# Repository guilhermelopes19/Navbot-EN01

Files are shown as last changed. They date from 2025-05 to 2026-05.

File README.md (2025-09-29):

# NavBot-EN01 Wheeled_leg-Robot

| Real Robot | 3D Design |
| --- | --- |
|  |  |

[Physical Demo Showcase](https://www.youtube.com/watch?v=H16f_6Kxv-E)  

[3D Demo Showcase](https://www.youtube.com/watch?v=OKktbMr_LOk)  

### Mechanical Structure Documentation
Under the ["Hardware/RebotModel"](Hardware/RebotModel) folder:
* The file "OriginalRobotModel.stp" is the robot model file.
* 3D printing, carbon fiber cutting, and CNC processing can all directly use the files in the corresponding folders.
* In ["BOM.xlsx"](Hardware/RebotModel/BOM.xlsx), there are other small components that need to be purchased.

### PCB Documentation

* The project requires the fabrication of four PCBs. Both the schematic and PCB source files are provided, and the design environment used is [easyeda](https://www.easyeda.com/).
Import project reference ["Hardware/PCB/README"](Hardware/PCB/README.md)
* The main control board is based on the ESP32, with the brushless motor driver chip being the L6234PD013TR. 
* The encoder chip used is the AS5600, communicating with the main control board via the I2C interface.
* The IMU used is the MPU6050 module, which shares the same I2C interface with the right-side encoder.
* The servo debugging board combines two UART serial lines into one signal line using time-division multiplexing for data transmission and reception.
* Two SH1.0mm 4PIN double-ended cables which need to be purchased separately，with a recommended length of 15cm. 

    | Wire Connection | 
    | ------------ |
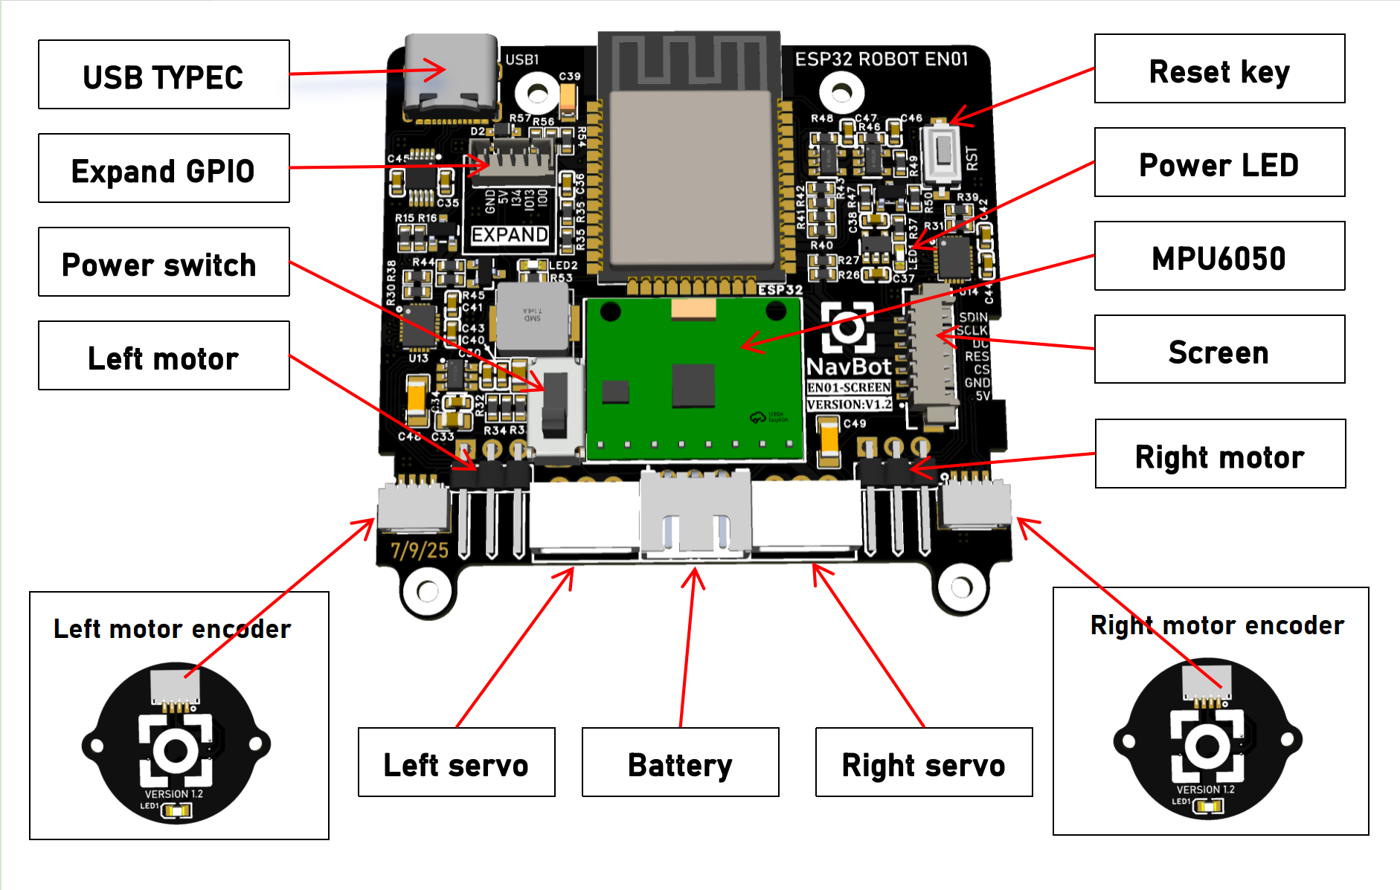
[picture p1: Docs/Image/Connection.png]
    |  |

### Source Code Usage

* Developed using the [Arduino IDE](https://www.arduino.cc/), which is user-friendly and widely adopted for embedded systems.
* The brushless motor drive for the wheels is based on [simpleFOC](https://www.simplefoc.com/#simplefoc_library).
* The left bus servo ID is 1, and the right is 2; the leg servo calibration value for achieving the mechanical limit in a fully squatted position is 2048; configuration is done using [FEETECH Debug Software](https://gitee.com/ftservo/fddebug).
* The [ESP32](https://www.espressif.com/sites/default/files/documentation/esp32_datasheet_en.pdf) itself has WiFi capabilities, with the webpage code stored in flash, transmitting JSON data via the WebSocket communication protocol.
* Please use the WebSocket library located in ["Src/libraries"](Src/libraries). The recommended esp32 version is 2.0.3.
* There are two WiFi models, AP mode and STA mode. AP mode uses the device as a wireless hotspot, and STA mode uses the device as a client to connect to an existing wireless network.
* Note: The WiFi band is 2.4GHz and cannot use the 5GHz band.

### The complete process of code compilation and download

1. Download and install [Arduino IDE](https://www.arduino.cc/), Recommend downloading Arduino IDE2。
2. Download the code of this repository.
3. After decompression, simply double-click the "Navbot-EN01/Src/wl_pro_robot/wl_pro_robot.ino" to open the project.

    | Open project | 
    | ------------ |
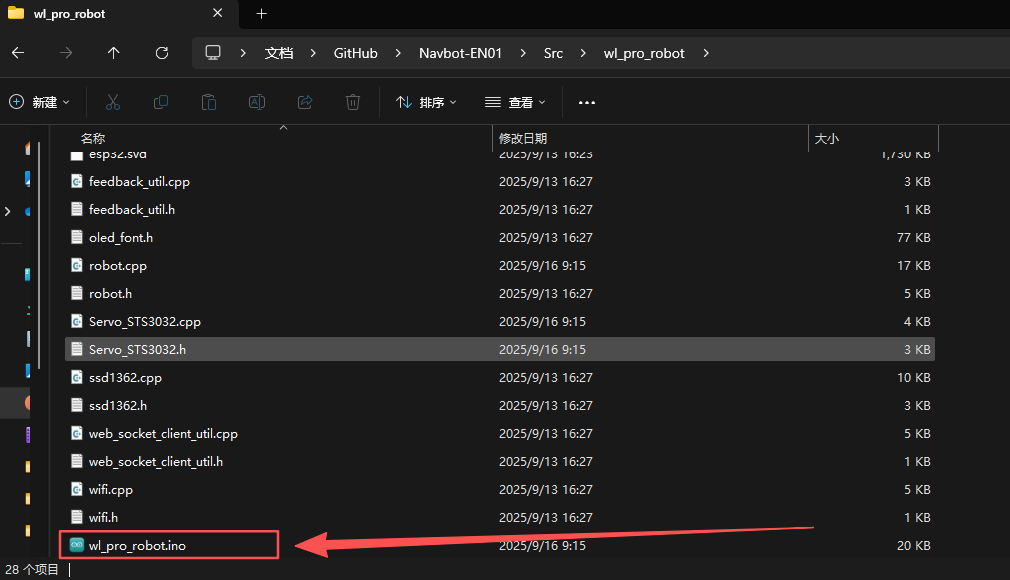
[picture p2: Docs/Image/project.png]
    |  |
4. Open the development board manager, search for esp32, select version 2.0.3, and click "Install".

    | Install the development package | 
    | ------------ |
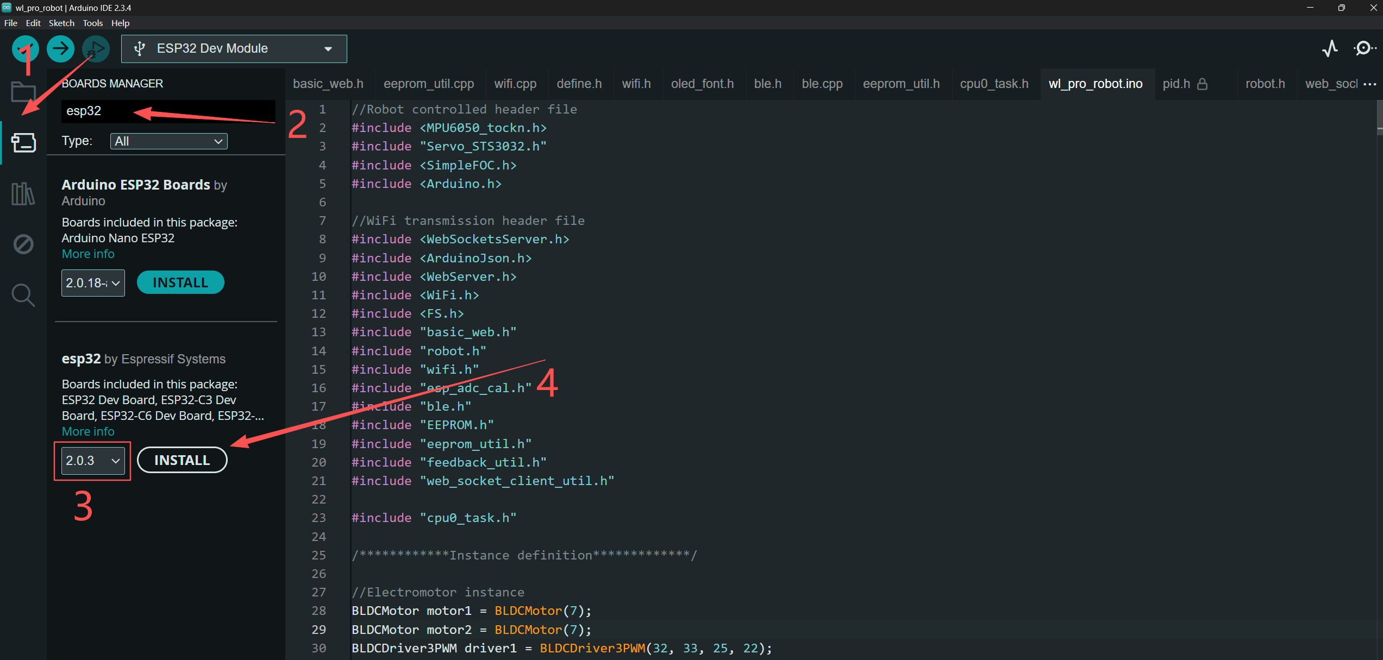
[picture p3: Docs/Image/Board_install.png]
    |  |
5. Click on "Sketch->Include library->Add.ZIP Library". Select the path "Navbot-EN01/Src/libraries/ArduinoJson.zip". Use the same method to add the remaining libraries as well.

    | Add libraries | 
    | ------------ |
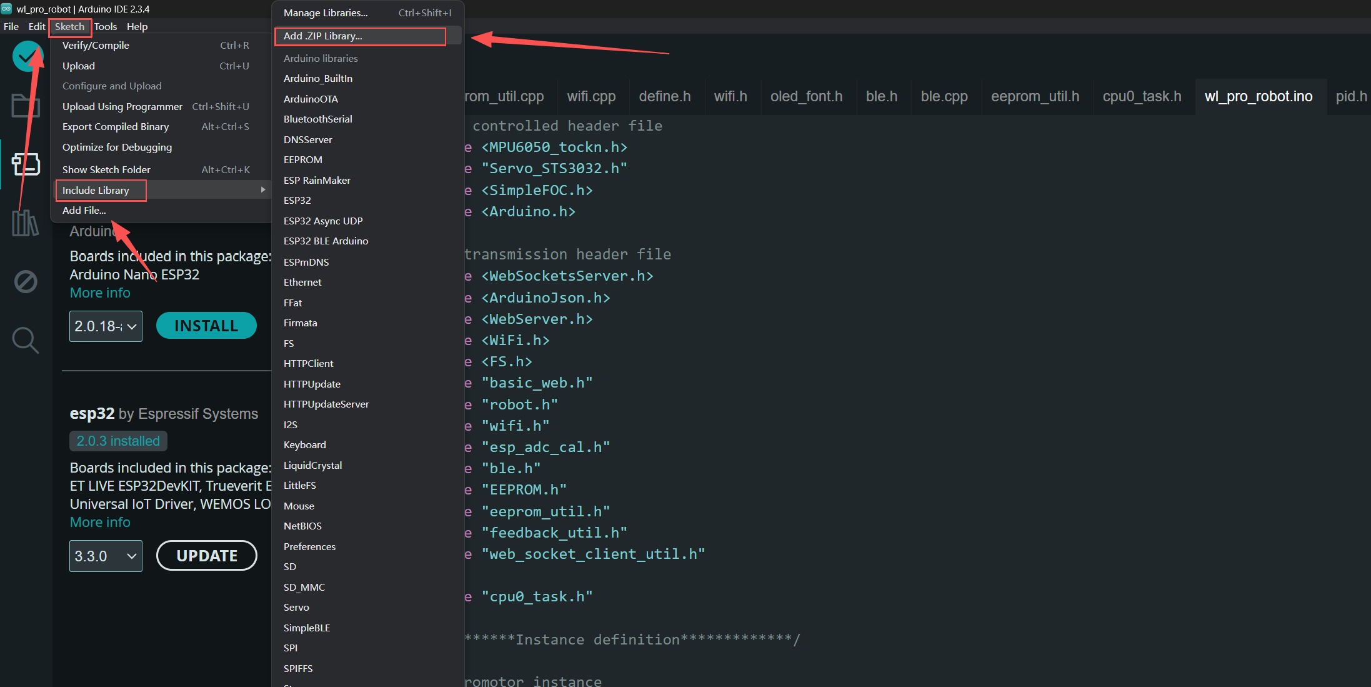
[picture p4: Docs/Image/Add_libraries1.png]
    |  |
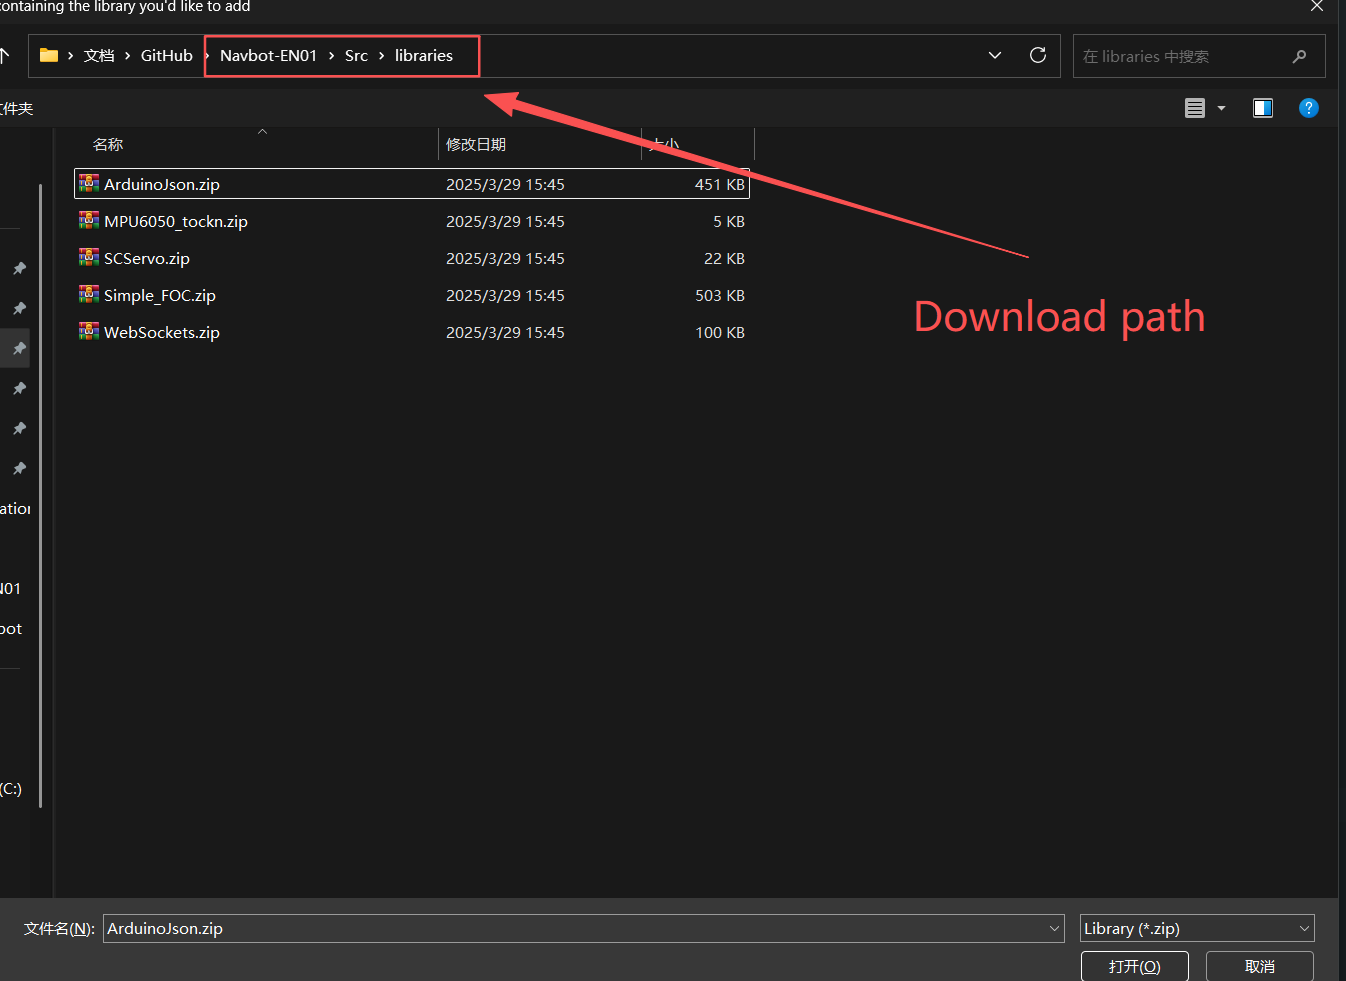
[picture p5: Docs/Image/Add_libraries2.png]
    |  |
6. Open the library manager, search for and download the "Queue" library.

    | Download queue library|
    | ------------ |
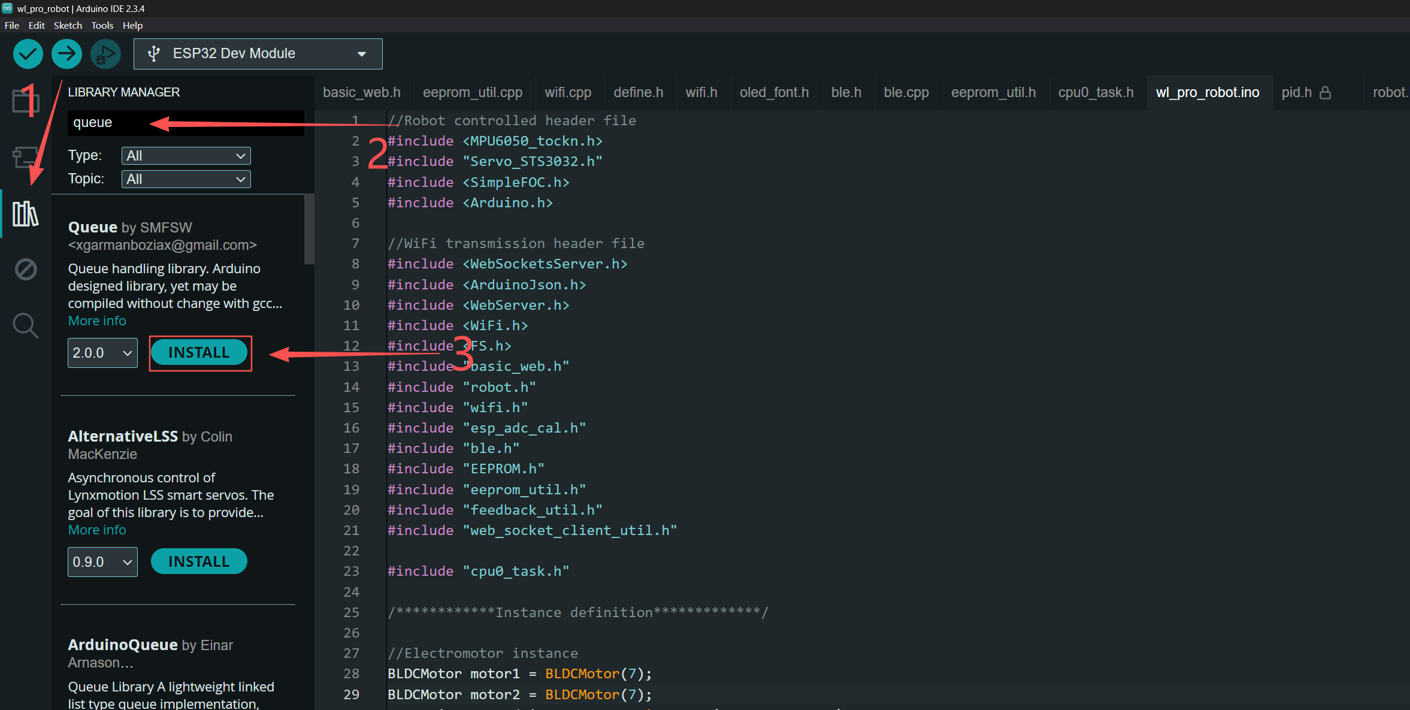
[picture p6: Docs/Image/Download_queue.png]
    |  |
7. Select the development board. In the search bar, search for "dev", select the ESP32 Dev Module, and choose the corresponding port. Note: If the machine is not connected, you don't need to select the port because there are no ports to choose from. The serial port numbers for each person may not be the same as the author's.

    | Select board |
    | ------------ |
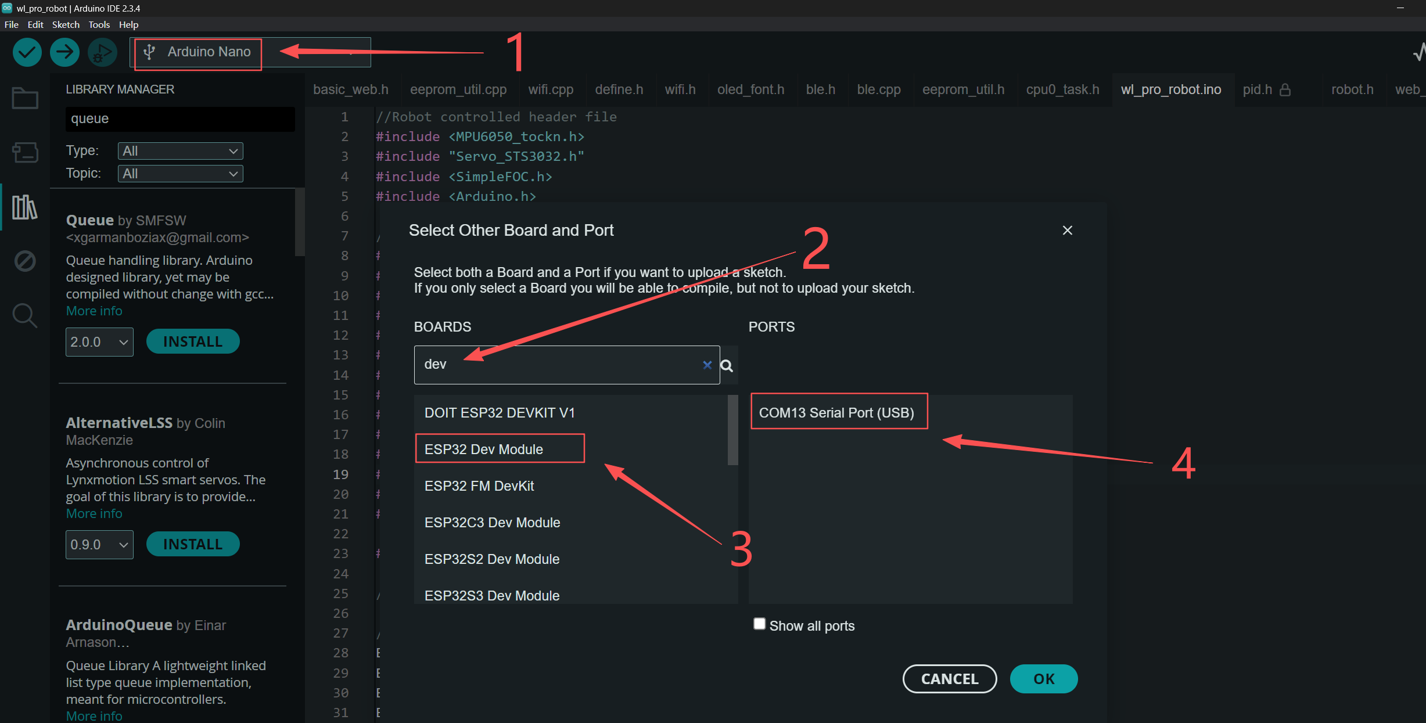
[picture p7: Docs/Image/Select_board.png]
    |  |
8. Change the partition scheme. The spiffs partition is currently used to store emoji files.
    | Modify the partition |
    | ------------ |
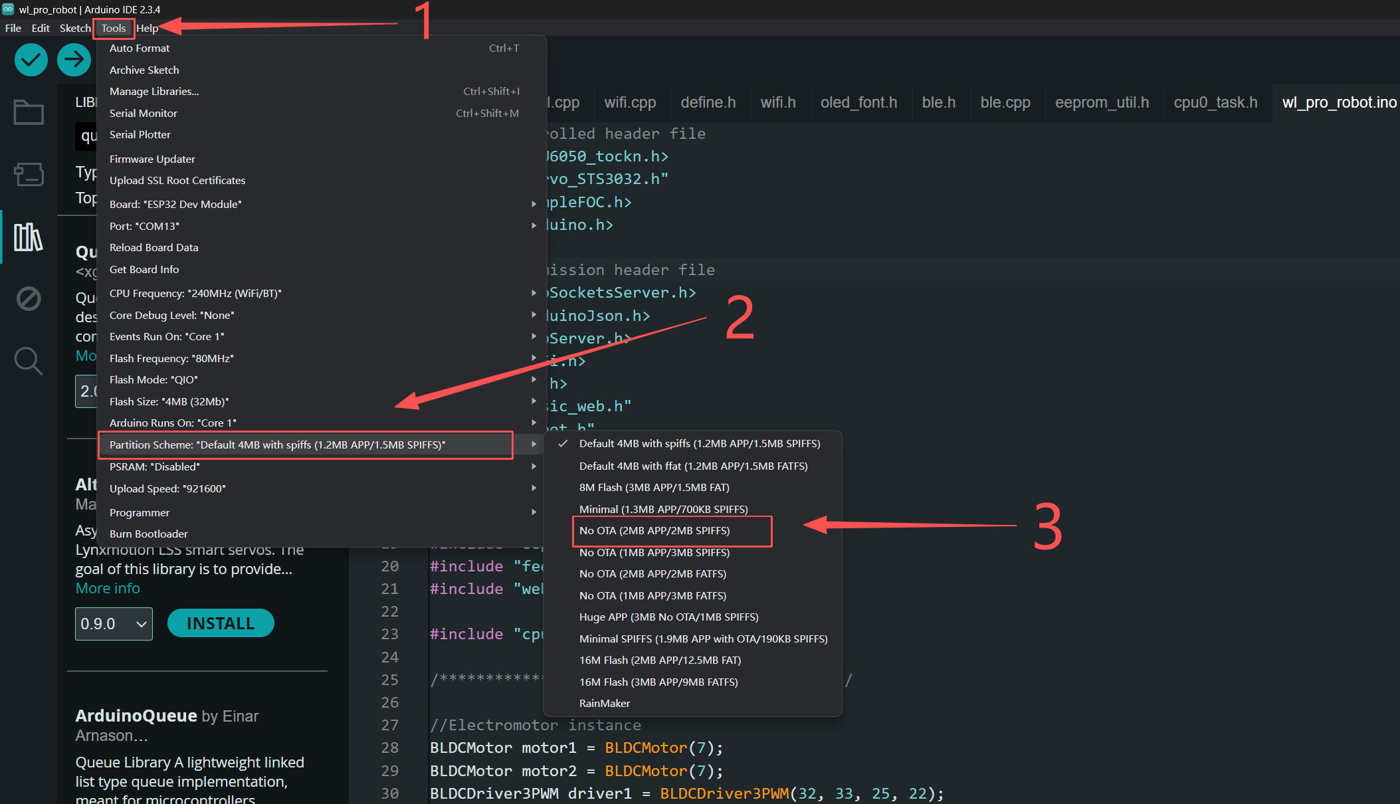
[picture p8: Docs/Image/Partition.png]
    |  |
9. Compile and download. Note: The first compilation may take a long time and is related to the computer configuration. The author's longest compilation time was 24 minutes.

### Implementation of expression function
* This version has achieved the function of expression linkage. This section mainly explains how to create expression files and upload them to the robot.

1. Prepare the document  
    Extract the Gif_to_Bin.zip file in the [Tools] folder. Then you will see a gif_to_bin.py script. At this point, it is recommended to place the GIF files to be converted in the same directory as the script. Next, you need to download Python 3 on your computer. After the download is complete, right-click and select Open in Terminal. Enter the following command 
    ```
    python .\gif_to_bin.py .\yourFile.gif 
    ```
    Then a "yourFile.bin" file will be generated, and this bin file will be uploaded to the esp32.

2. Upload files

    ESP32 stores emoji files in SPIFFS. For information on how to upload files to SPIFFS, please refer to this repository [https://github.com/me-no-dev/arduino-esp32fs-plugin](https://github.com/me-no-dev/arduino-esp32fs-plugin)。

    Unfortunately, Arduino IDE 2 does not support plugin functionality. Therefore, the author downloaded Arduino IDE 1 instead, which enables a more convenient file upload process. It is also important to note that when uploading the files, please ensure that the partition scheme used during the upload is the same as the one specified in the download procedure.

### Usage Instructions

1. Connect the battery's XH2.54 plug to the rear interface of the main control board and turn on the switch to power the robot.
2. A red light on the main board will indicate that the power is on.
3. The wheels will start FOC motor initialization, with the wheels moving slightly and the legs starting to move.
4. If the battery charge is sufficient, the blue LED on the main control board will light up. If it does not light up, charging is needed.
5. After this process is complete, press the EN button on the main control board to restart, and you can then connect to the robot's WiFi network starting with navbot_en01. The password is 12345678.
6. Open a browser connected to the robot's WiFi network and navigate to 192.168.1.11. The remote control interface is compatible with Android, iOS, Windows, Linux, macOS, etc., and it is recommended to use Chrome or Firefox.
7. Manually stabilize the robot, with the wheels slightly touching the ground. Click the "Robot go!" button on the web page, and the robot will stand up. You can then control the robot's movement using the joystick.

### Discord link
| Link: [https://discord.gg/cWGK4yER62](https://discord.gg/cWGK4yER62)        |
| :------------: |
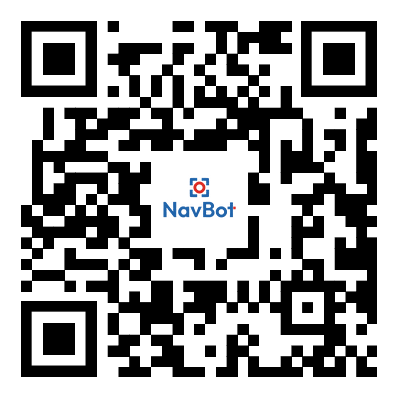
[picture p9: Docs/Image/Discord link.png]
|  |

### Guidance Viedeo & Blog
Video: [DIY Education Nano 01 - Modular Wheel-Leg Robot for STEM](https://www.youtube.com/watch?v=cPD-h2ZjIqo)

Blog:  [Building a Tabletop Wheel-Legged Robot from Scratch](https://frankfu.blog/embodied-ai-robot/building-a-tabletop-wheel-legged-robot-from-scratch/)  

Thanks for Mu Shibo & Li Yufeng：The original repository https://github.com/MuShibo/Micro-Wheeled_leg-Robot

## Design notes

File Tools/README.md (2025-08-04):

Servo motor debugging:
Write the SteeringEngineDebug code into the mainframe, then open the folder starting with "FD", open FD.exe, and set the baud rate to 1000000.
Attention!!! The first calibration of the servo motor may cause a bus conflict due to the same ID. In this case, you need to unplug the other servo motor.

Writing emoticons into ESP32:
1. Prepare the GIF file, convert each frame to a bitmap modulus using gif_to_bin, and finally generate a.bin file. Create a new "data" folder in the main program directory, and copy the bin file of the emoji package to the "data" folder.
2. You need to install Arduino IDE 1.8. Since the spiffs flashing plugin used does not support Arduino 2 version, the plugin's compressed package name is: ESP32FS-1.1. Installation method can be referred to https://github.com/me-no-dev/arduino-esp32fs-plugin
3. After the above installation, open the project in Arduino IDE 1.8, then click the menu bar's "tool>ESP32 Sketch Data Upload", and the plugin will flash the contents in the "data" folder to the esp32.

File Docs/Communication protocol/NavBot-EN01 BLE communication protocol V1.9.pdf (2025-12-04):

# NAVBOT-EN01 BLE communication protocol

Table of Contents

## Revision History

# DOCUMENT HISTORY

SOFTWARE REVISION | CHANGES MADE | REVISION DATE | EDITED BY
1.0 | Add BLE protocol | 5/1/2025 | XiaoleChen
1.1 | Modify the document structure,and add WIFI connection command | 5/19/2025 | XiaoleChen
1.2 | Correct the errors in version 1.1 | 5/23/2025 | XiaoleChen
1.3 | Add JSON and define the protocol for reading status. | 7/3/2025 | XiaoleChen
1.4 | Add and modify JSON key-value pairs | 7/17/2025 | XiaoleChen
1.5 | Add servo calibration instructions | 7/22/2025 | XiaoleChen
1.6 | Improve the JSON description and add the option to modify the device name | 7/25/2025 | XiaoleChen
1.7 | Add JSON protocol and call expression | 8/26/2025 | XiaoleChen
1.8 | Separate the expression acquisition into a new protocol, modify the member names and default values of sys_web_socket_server; add set_openAI_token. JSON protocols set_cloud_token and | 9/3/2025 | XiaoleChen
1.9 | Increase the out-of-control angle and recovery angle adjustment. | 10/22/2025 | XiaoleChen

## 1. BLE information

BLE NAME :
navbot_en01-******

Service UUID:
6E400011-B5A3-F393-E0A9-E50E24DCCA9E

Send data characteristic UUID: 6E400012-B5A3-F393-E0A9-E50E24DCCA9E

Receive data characteristic UUID: 6E400013-B5A3-F393-E0A9-E50E24DCCA9E

## 2. Data frame agreement

Byte | Name | Description
Byte 1 | Header1 | Fixed 0x55
Byte 2 | Header2 | Fixed 0xAA
Byte 3 | Command | The control command of this data frame, reference 3.Command
Byte 4 | Remaining | The number of frames remaining after synthesizing the complete data
Byte 5 | Null | Retain
Byte 6 ~Byte 20 | Data

## 3. Command

The third byte is the command byte, which determines the function of the data from the 6th to the 20th byte. The current definition is as follows:
Command | Name | Explanation
0x00 | CMD_MANEUVER CMD_WIFI | Robot maneuver, at this time the meaning of the data frame reference 3.0.CMD_MANEUVER. 0x01
| CMD_JSON | Connect the robot to the wireless network. The data frame refers to 3.1.CMD_WIFI. 0x02
| | JSON transmission, byte 6 to byte 20 represent the JSON body. Refer to 3.2. CMD_JSON

## 3.0. CMD_MANEUVER

When byte3(command) is equal to 0x00, it indicates that bytes 6 to 20 control the maneuverability of the robot. At this time, the data should follow the following rules:
Byte | Name | Description
Byte 1 | Header1 | Fixed 0x55
Byte 2 | Header2 | Fixed 0xAA
Byte 3 | Command | 0x00
Byte 4 | Remaining | 0x00
Byte 5 | Null | Retain
Byte 6 | roll | Rolling Angle, value range -30 to 30. Byte 7 | height | The height of the robot, with a value range of 32 to 85. Byte 8 | linear_H
| linear_L | Linear speed, with a value range of -200 to 200. Byte 9
Byte 10 | angular stable | The angular velocity of the robot, with a value range of -100 to 100. Byte 11 The stable state of the robot: 1 on, 0 off
Byte 12 | mode | Fixed 0x01
Byte 13 | dir | The movement direction of the robot is defaulted to 0, jump:1
Byte 14 | joy_y joy_x | The Y-axis data of the joystick, with a value range of -100 to 100. Byte 15 The X-axis data of the joystick, with a value range of -100 to 100. Byte 16
~ Byte 20 | Null | Idle

## 3.0.1. Data frame demonstration：

55 AA 00 00 00 00 26 0000 00 01 00 00 00 00 00 00 00 00 00 // height = 0x26(38), stable = 1 After sending this instruction, the robot starts and the leg height is 38mm. 55 AA 00 00 00 00 30 0000 00 01 00 00 00 00 00 00 00 00 00 // height = 0x30(48), stable = 1 ,After sending this instruction, the robot starts and the leg height is 48mm. 55 AA 00 00 00 00 30 0000 00 00 00 00 00 00 00 00 00 00 00 // height = 0x26(38), stable = 0 ,After sending this instruction, the robot stops and the leg height is 48mm. 55 AA 00 00 00 00 26 0000 00 01 00 00 00 05 00 00 00 00 00 // height = 0x26(38), stable = 1 ,joy_y = 0x05(5) , After sending this instruction, the robot moves forward at a speed of 5. 55 AA 00 00 00 00 26 0000 00 01 00 00 00 FA 00 00 00 00 00 // height = 0x26(38), stable = 1 ,joy_y = 0xFA(-5), After sending this instruction, the robot moves backward at a speed of 5. 55 AA 00 00 00 00 26 0000 00 01 00 00 00 00 05 00 00 00 00 // height = 0x26(38), stable = 1 ,joy_x = 0x05(5) , After sending this instruction, the robot rotates clockwise with an angular velocity of 5. 55 AA 00 00 00 00 26 0000 00 01 00 00 00 00 FA 00 00 00 00 // height = 0x26(38), stable = 1 ,joy_x = 0xFA(-5), After sending this instruction, the robot rotates counterclockwise with an angular velocity of 5. 55 AA 00 00 00 00 26 0000 00 01 00 00 01 00 00 00 00 00 00 // height = 0x26(38), stable = 1 ,dir = 0x01, sending this instruction, the robot jumps and is ready. 55 AA 00 00 00 00 26 0000 00 01 00 00 00 00 00 00 00 00 00 // height = 0x26(38), stable = 1 ,dir = 0x00, After sending this instruction, the robot jumps in place.

## 3.1. CMD_WIFI

When byte3(command) is equal to 0x01, The next 6 to 20 bytes are the information of the wifi, which includes the SSID (wifi name) and password of the wifi. The wifi name and password should be in the ASCLL character set. Then, the structure of the data should follow the following rules:

Byte | Name | Description
Byte 1 | Header1 | Fixed 0x55
Byte 2 | Header2 | Fixed 0xAA
Byte 3 | Command | 0x01
Byte 4 | Remaining Null | * Byte 5 Idle
Byte 6 ~Byte 20 | data | This piece of data stores the name and password of the wifi, with the name first and the password second, separated by a TAB(‘\t’,ASCLL=9) character in between. 3.1.1.Data frame demonstration The data demonstration format is listed

## 3.1.1. Data frame demonstration：

55 AA 01 00 00 6E 61 76 62 6F 74 09 49 4A 4B 4C 4D 4E 4F 50

The example data above is a complete BLE data frame; Starting from byte 6 to byte 11, they are all valid ASCLL characters. However, byte 12 (already marked) is 0x09, which represents a TAB character in ASCLL encoding. Therefore, before this byte (0x09), it should be the wifi name, and after this byte (0x09), it is the password. Then we can come up with the wifi name as "navbot" and the password as "12345678".

## 3.2. CMD_JSON:

This command data frame format is:
Byte | Name | Description
Byte 1 | Header1 | Fixed 0x55
Byte 2 | Header2 | Fixed 0xAA
Byte 3 | Command | 0x02
Byte 4 | Remaining Null | * Byte 5 Idle

Byte 6 ~Byte 20
Body data JSON body,Transmission can be subcontracted. 3.2.1. JSON protocol :

Using the key name "type" to distinguish different commands, the currently defined values for the "type" key are as follows:
Type value：(string) | explain
“set_wifi” | Set up Wi-Fi information, refer to 3.2.1.1
“sys_web_socket_server” | Set up the cloud server, referring to 3.2.1.2
“sys_restart” | Restart the robot, refer to 3.2.1.3
“get_device_info” | Obtain robot information, refer to 3.2.1.4
“off_servo” | Shut off the steering gear, refer to 3.2.1.5
“on_servo” | Start the servo motor, refer to 3.2.1.6
“calibrate_servo” | Calibrate the servo motor based on the current status, referring to 3.2.1.7
“set_name” | Modify the alias of the device, merely as a means of identification. referring to 3.2.1.8
“show_expression” | Make the robot display the specified expression. referring to 3.2.1.9
“get_expression” | Obtain the available expression files inside the robot,referring to 3.2.1.10
“set_cloud_token” | Set the token that links to the cloud server, referring to 3.2.1.11
“set_openai_token” | Set up a token linked to OpenAI, referring to 3.2.1.12
”set_uncontrolablle_angle” | The machine has tilted to an out-of-control angle threshold. referring to 3.2.1.13
”set_recovery_angle” | The angle for restoring control and balance after the robot loses control. referring to 3.2.1.14

### 3.2.1.1. sys_wifi

{ “type”:”sys_wifi”, “ssid”:”*************”, “password”:”***********”, “state”: “server”, // or “client”; or ”close”

}

### 3.2.1.2. sys_web_socket_server

{ “type”:”sys_web_socket_server”, “host”:”hub.navbot.com”, “port”:443, //int “path”: “/ws/****”

}

### 3.2.1.3. sys_restart

{ “type”:”sys_restart”

}

### 3.2.1.4. get_device_info

The upper computer sends:
{ “type”:”get_device_info”

}
Robot reply:
{ | “type”: | “get_device_info”, “pcb_version”: | double, “battery_level”: double, “battery_voltage”: double, “centigrade”: | double, “name”: | string, “charge”: | bool, “IP”: | string, “cloud_token”: | string,

“openAI_token”: string, “mac”: | string

“uncontrolablle_angle”: unsigned int, “recovery_angle”: unsigned int

}

### 3.2.1.5. off_servo

{ “type”:”off_servo”

}

### 3.2.1.6. on_servo

{ “type”:”on_servo”

}

### 3.2.1.7. calibrate_servo

{ “type”:”calibrate_servo”

}

### 3.2.1.8. set_name

{ “type”:”set_name”, “name”: string

}

### 3.2.1.9. show_expression

{ “type”:”show_expression”, “file”: “*.bin”, “time”: int

}
First, you need to obtain the available emoji files,Refer to the next command 3.2.1.10 . Then, after "file", enter the file name; "time" indicates the duration, and if the value is 0, it means the display will continue indefinitely. 3.2.1.10. get_expression

The upper computer sends:
{ “type”:”get_expression”

}
Robot reply:
{ | “type”: | “get_expression”, “expression”: | [“*.bin”, “*.bin”, “*.bin”, | ]

}

### 3.2.1.11. set_cloud_token

The upper computer sends:
{ “type”:”set_cloud_token”, “token”: ”****”

}

### 3.2.1.12. set_openai_token

The upper computer sends:
{ “type”:”set_openai_token”, “token”: ”****”

}

### 3.2.1.13. set_uncontrollable_angle

The upper computer sends:
{ “type”:”set_uncontrolablle_angle”, “angle”: unsigned int // range 10-90

}

### 3.2.1.14. set_recovery_angle

The upper computer sends:
{

“type”:”set_recovery_angle”, “angle”: unsigned int //range 10-90 }

## 4. Subcontracting

Since the BLE Bluetooth data frame is only 20 bytes, excluding the first 5 bytes that have been occupied, the valid data provided to the user is only 15 bytes. However, in many scenarios, the data is far greater than 15 bytes. For instance, the characters of the wifi name and password

are often larger than 15 bytes. At such times, we can use the 4th byte (the Remaining part) for Subcontracting operations. It indicates how many frames of data that follow need to be merged with this frame of data, as shown in the following example:

Suppose the wifi name is “American_network_ABCDEFG” and the password is “0123456789”, Then the following data frames should be sent:

55 AA 01 02 00 41 6D 65 72 69 63 61 6E 5F 6E 65 74 77 6F 72
55 AA 01 01 00 6B 5F 41 42 43 44 45 46 47 09 30 31 32 33 34
55 AA 01 00 00 35 36 37 38 39 00 00 00 00 00 00 00 00 00 00

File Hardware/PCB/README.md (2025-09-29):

### Begin

1. visit website [https://www.easyeda.com](https://www.easyeda.com)
2. On the main page of the website, click "Design online" and select "Pro Edition"

    | Add libraries | 
    | ------------ |
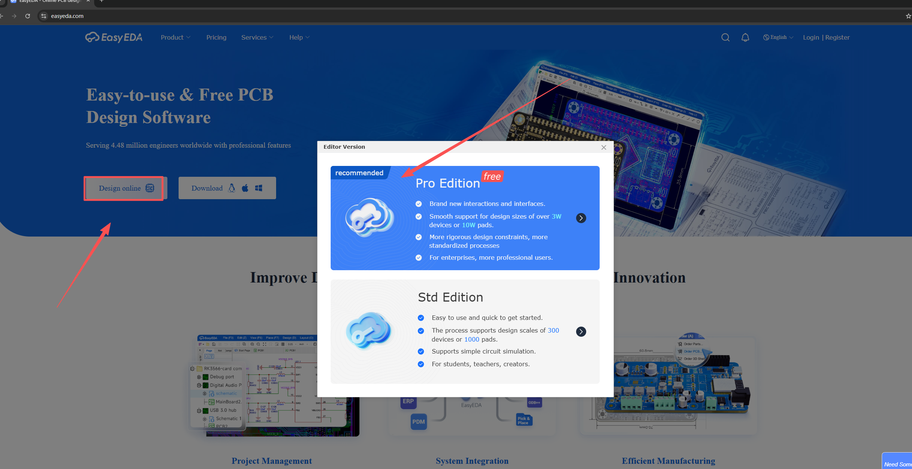
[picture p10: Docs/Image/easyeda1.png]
    |  |

3. At this point, you need to log in.

    | Add libraries | 
    | ------------ |
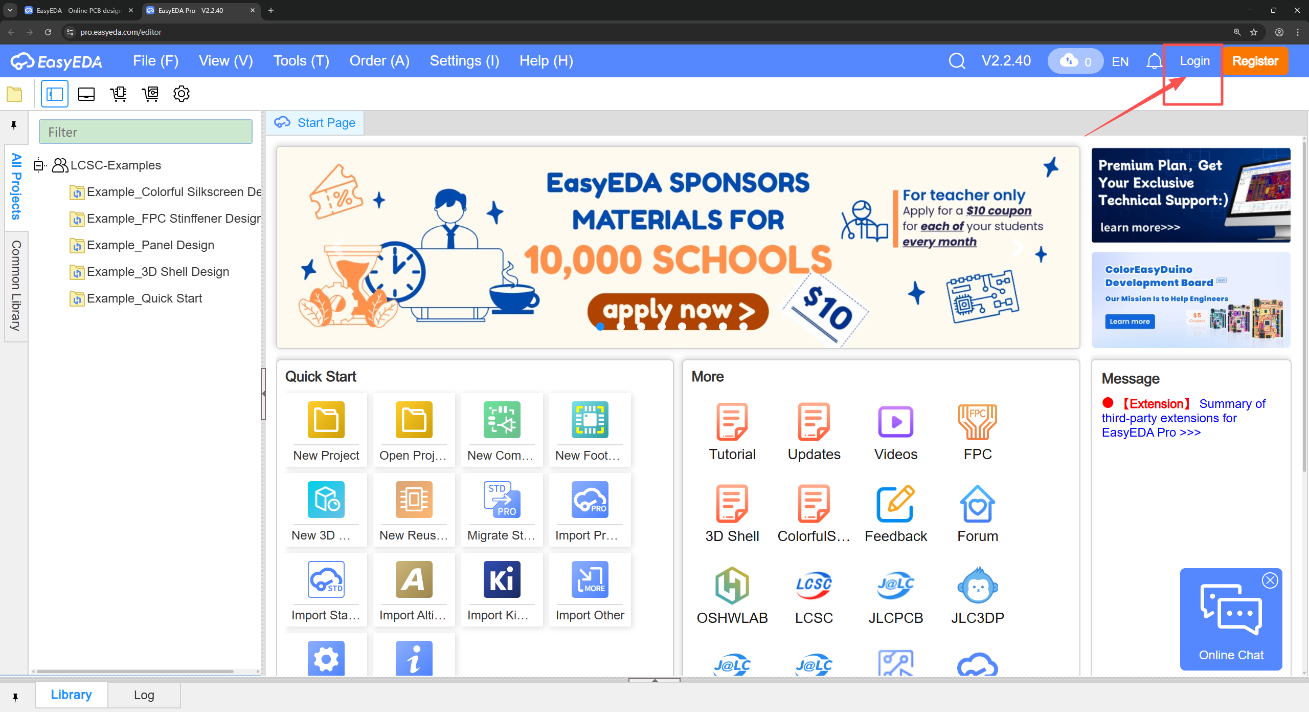
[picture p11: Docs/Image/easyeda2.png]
    |  |
4. File->Import->JLCEDA(Professional), select NavBot-EN01.epro

    | Add libraries | 
    | ------------ |
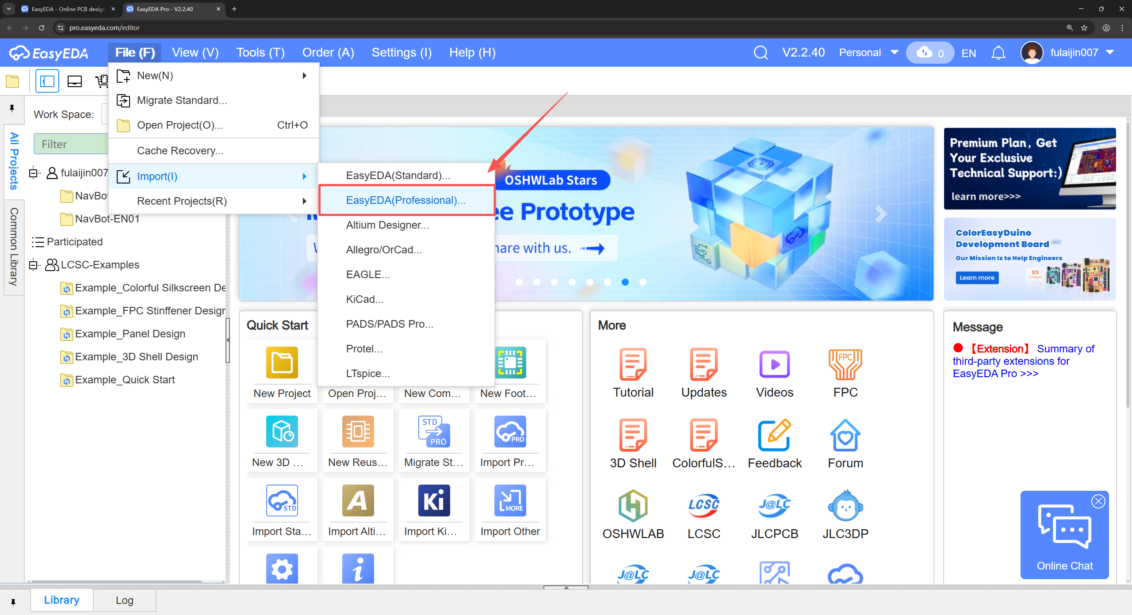
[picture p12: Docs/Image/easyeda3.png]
    |  |

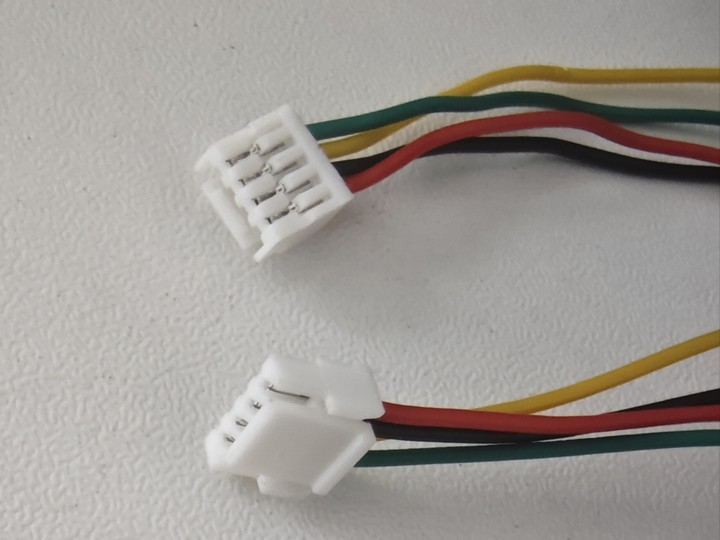
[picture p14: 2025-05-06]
Docs/Image/wire.png

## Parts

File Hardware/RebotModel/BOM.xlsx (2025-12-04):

Part Name | Recommended Purchase Link | Specifications | Quantity
Servo | https://www.amazon.com/magnetic-rotating-minibus-steering-black/dp/B0BP645PF9 | ST3032 | 2
Motor | https://www.amazon.com/Fityle-Gimbal-Brushless-100-200g-Quadcopter/dp/B07JLSL8ZV | 2208，< 200kv | 2
Neodymium Magnet | https://www.amazon.com/TRYMAG-Magnets-Neodymium-Whiteboard-Billboard/dp/B09SL2K4BP | w4*h1 | 2
Battery | https://item.taobao.com/item.htm?id=559166020526 | 1000mah | 1
Screw M2*4 | https://www.amazon.com/iexcell-Thread-Socket-Screws-Finish/dp/B0D4JM92FW | M2*4 | 20
Screw M2*6 | https://www.amazon.com/iexcell-Thread-Socket-Screws-Finish/dp/B0D4JMMJ9M | M2*6 | 10
Screw M2.5*5 | https://www.amazon.com/iexcell-Thread-Socket-Screws-Finish/dp/B0DDXRMGCW | M2.5*5 | 10
Screw M3*6 | https://www.amazon.com/iexcell-Thread-Socket-Screws-Finish/dp/B07GGXKW1Y | M3*6 | 4
BigHead Screw M2*6 | https://detail.tmall.com/item.htm?id=722946822369&spm=a1z09.2.0.0.6f8c2e8daIyqdB&_u=k2st8hc21ee3 | M2*6 | 4
Nut M2 | https://www.amazon.com/pouilzx-Carbon-Steel-Hexagon-200pcs/dp/B0CMG7Q27P | M2 | 10
Screw M2.3*15 | https://item.taobao.com/item.htm?spm=a1z09.2.0.0.6f8c2e8daIyqdB&id=538025764032&_u=k2st8hc217d7 | M2.3*15 | 2
Earings 3-6-2 | https://www.amazon.com/Hobbypark-Bearings-Shielded-Quadcopter-Helicopter/dp/B019F2ZH92 | 3*6*2 | 4
Earings 4-7-2.5 | https://www.amazon.com/4x7x2-5-Shielded-Precision-Miniature-Bearings/dp/B085RD75QY | 4*7*2.5 | 4
Cylindrical Pin 4x12 | https://www.amazon.com/uxcell-Stainless-Cylindrical-Support-Elements/dp/B07YKYJZ63 | 4*12 | 2
Brass Standoff M2*8+3 | https://www.amazon.com/MECCANIXITY-Standoffs-Assortment-Raspberry-Motherboard/dp/B0FH1FTF5J | M2*8+3 | 2
Brass Standoff M2*25+4 | https://www.amazon.com/PATIKIL-Standoff-Quadcopter-Motherboard-Computer/dp/B0DWF384DG | M2*25+4 | 2
Brass Standoff M2*8 | https://www.amazon.com/uxcell-Straight-Pillar-Standoff-M2x3x8mm/dp/B07H3SR8XX | M2*8 | 2
Brass Standoff M2*3*3 | https://www.amazon.com/uxcell-116pcs-Straight-Standoff-M2x3x3mm/dp/B07H3XJ7BB?sp_csd=d2lkZ2V0TmFtZT1zcF9hdGY | M2 w3*h3 | 4
Tire（Round Silicone Ring） | https://www.amazon.com/Rubber-Assorted-Camping-Survival-Supplies/dp/B0BX4CYWB7 | Diameter 25 Width 10mm Black | 2
OLED | https://item.taobao.com/item.htm?id=769782683401 | 1.21 inches | 1
sh1.0 4P | https://www.amazon.com/Pre-Crimped-Connectors-SPRacingF3-Omnibus-Silicone/dp/B07PDQKHJ2 | 150mm | 2
MX1.27 7P | https://www.amazon.com/HFHYDZSW-MX1-25-1-25mm-Connector-Head_10PCS_7P/dp/B0DSTVJBH2 | 10mm | 1

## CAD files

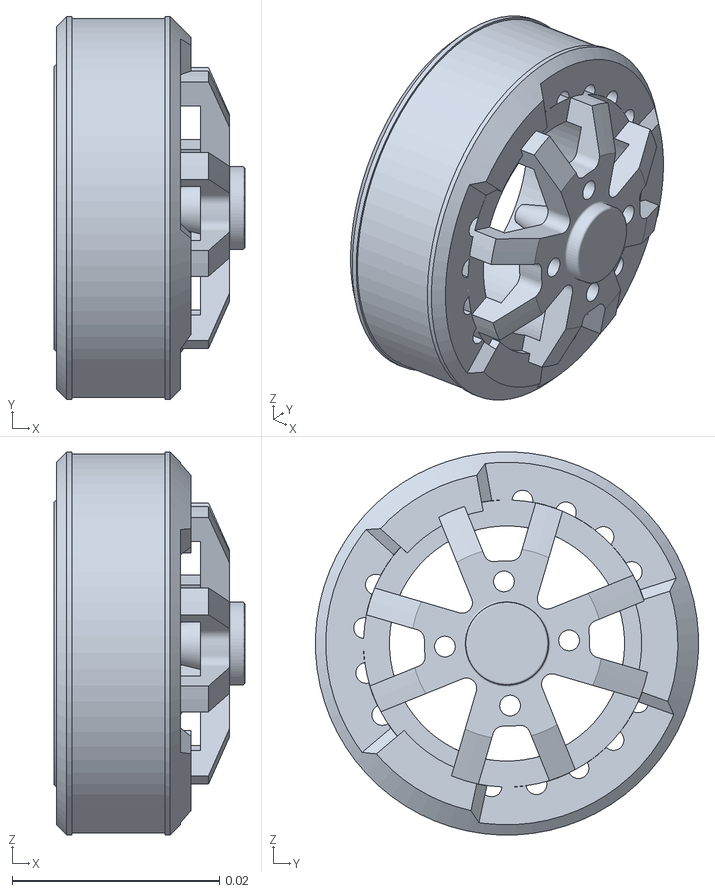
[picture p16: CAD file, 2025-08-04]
Docs/Simulator/navbot/merged/wheel_motor_2_visual.obj
0.0184 x 0.037 x 0.037

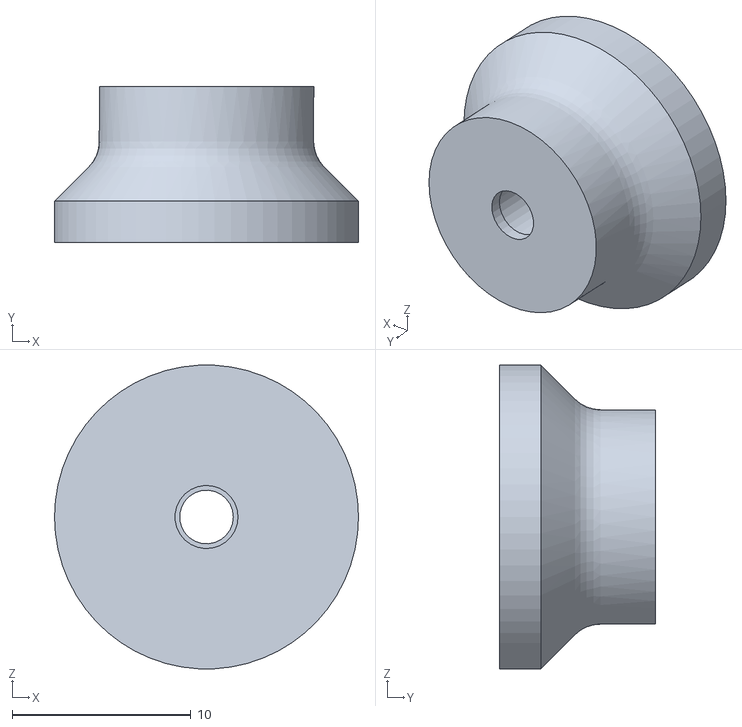
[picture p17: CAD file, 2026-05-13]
Hardware/RebotModel/3D_print/ColumnCover x2.stl
17.0 x 8.70 x 17.0

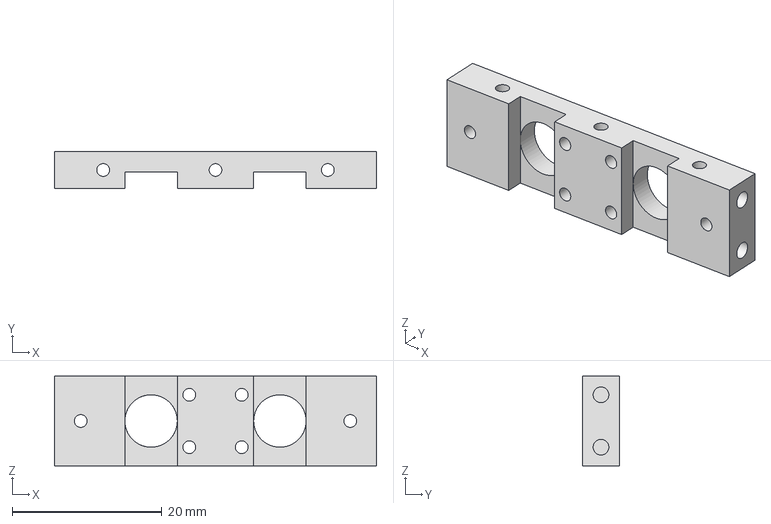
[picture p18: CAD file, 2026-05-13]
Hardware/RebotModel/CNC/MotorBase-Aluminum6061.stp
43.0 x 5.00 x 12.0 mm

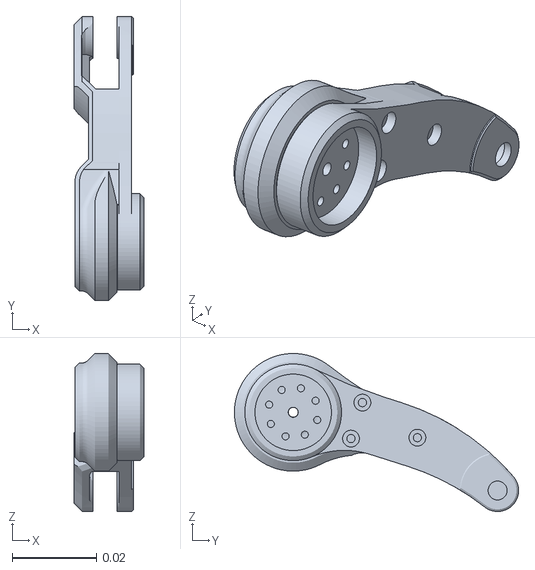
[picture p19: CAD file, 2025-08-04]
Docs/Simulator/navbot/merged/leg_left_visual.obj
0.0168 x 0.0676 x 0.0376

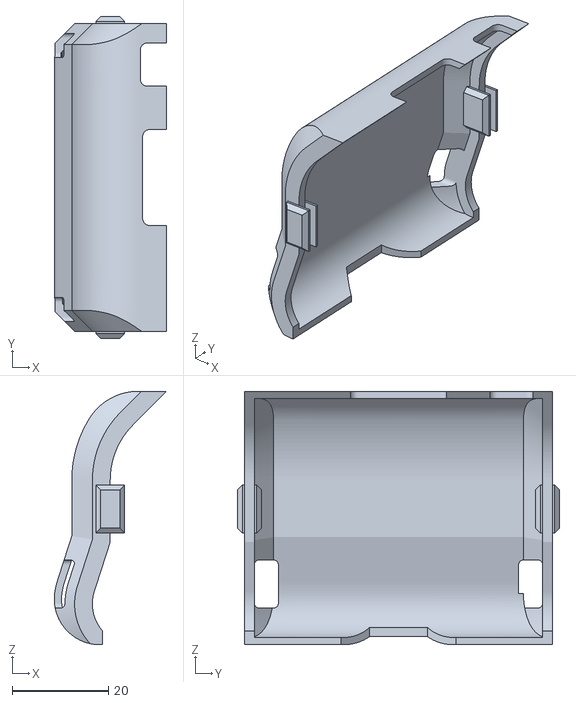
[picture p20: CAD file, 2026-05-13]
Hardware/RebotModel/3D_print/PCBCover(optional).stl
23.4 x 67.0 x 52.7

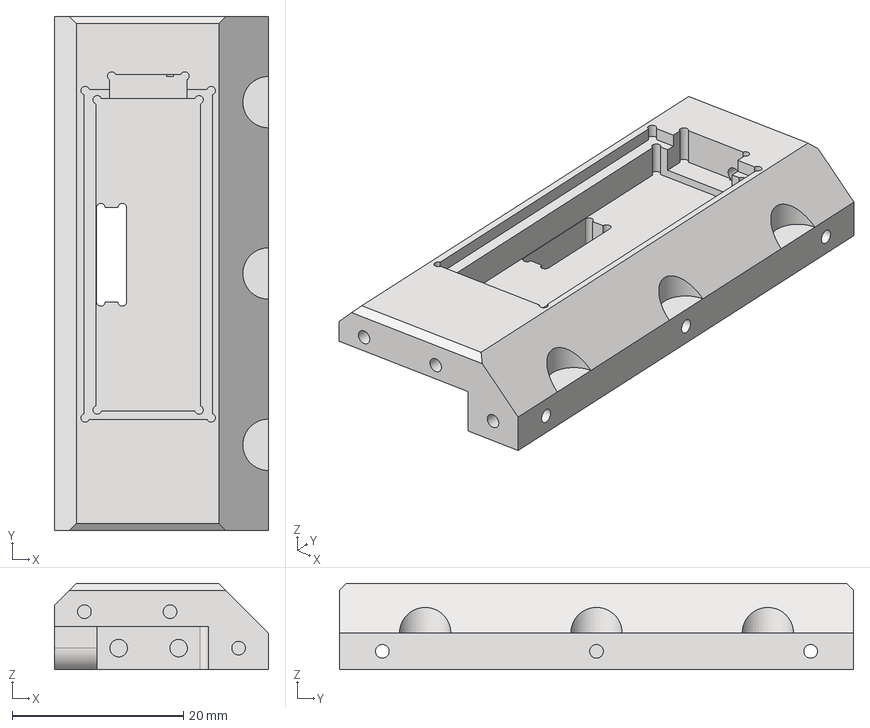
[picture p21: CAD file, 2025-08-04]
Hardware/RebotModel/CNC/BodyBasc-Aluminum6061.stp
25.0 x 60.0 x 10.0 mm

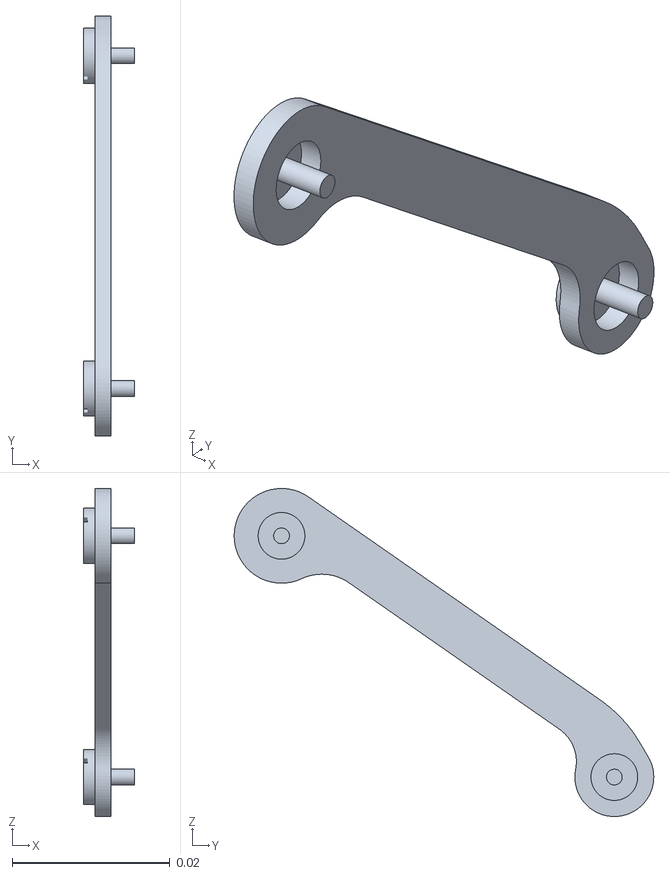
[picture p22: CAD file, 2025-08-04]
Docs/Simulator/navbot/merged/link_visual.obj
0.0065 x 0.0532 x 0.0416

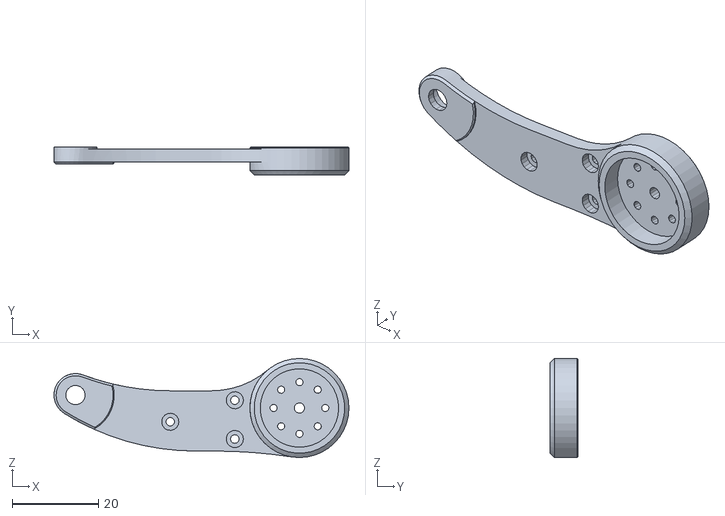
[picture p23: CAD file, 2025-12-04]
Hardware/RebotModel/3D_print/Thigh_R x1.stl
68.5 x 6.50 x 23.0

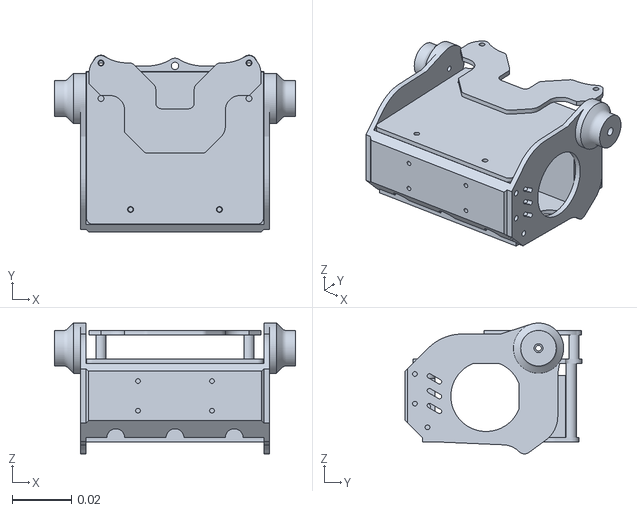
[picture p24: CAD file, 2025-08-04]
Docs/Simulator/navbot/merged/base_visual.obj
0.0814 x 0.0597 x 0.0442

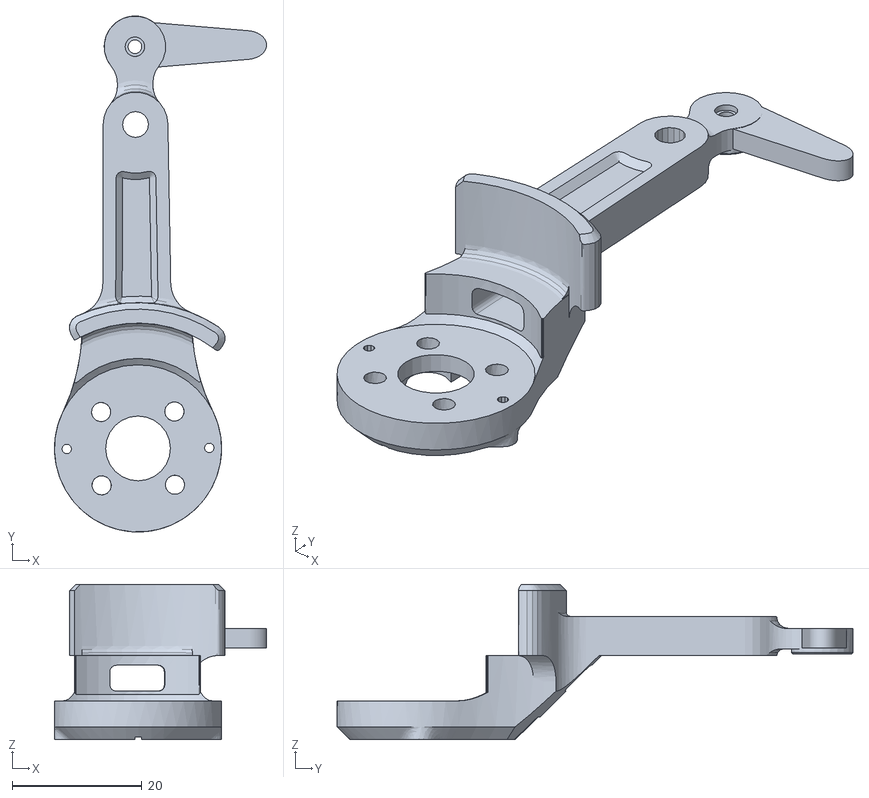
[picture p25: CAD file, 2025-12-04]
Hardware/RebotModel/3D_print/Calf_L x1.stl
32.7 x 79.6 x 24.0

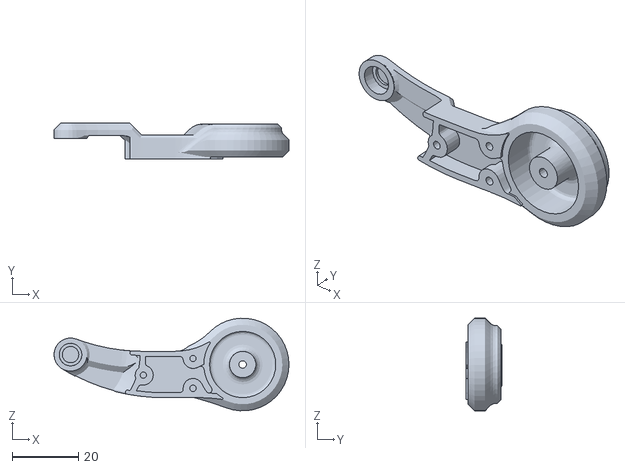
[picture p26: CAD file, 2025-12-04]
Hardware/RebotModel/3D_print/ThighCover_R x1.stl
71.0 x 10.8 x 28.0

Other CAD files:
Hardware/RebotModel/CarbonFiberPanels/Panel.dwg
Docs/Simulator/navbot/merged/link_2_visual.obj
Docs/Simulator/navbot/merged/leg_right_visual.obj
Hardware/RebotModel/3D_print/ThighCover_L x1.stl
Docs/Simulator/navbot/merged/wheel_motor_visual.obj
Hardware/RebotModel/3D_print/Thigh_L x1.stl
Hardware/RebotModel/3D_print/Calf_R x1.stl
Hardware/RebotModel/3D_print/magnet_frame.stl
Hardware/RebotModel/3D_print/new_curs1.stl
Hardware/RebotModel/3D_print/new_curs2.stl
Hardware/RebotModel/3D_print/new_wheel.stl

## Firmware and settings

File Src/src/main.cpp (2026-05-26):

//Robot controlled header file
#include <SimpleFOC.h>
#include <Arduino.h>
//#include <MPU6050_tockn.h>
// #include "Servo_STS3032.h"
//#include <MPU9250_asukiaaa.h>
#include <IMU.h>
//#include <BitBang_I2C.h>
#include <Servos.h>

//WiFi transmission header file
#include <WebSocketsServer.h>
#include <ArduinoJson.h>
#include <WebServer.h>
#include <WiFi.h>
#include <FS.h>
#include "basic_web.h"
#include "robot.h"
#include "wifi_robot.h"
#include "esp_adc_cal.h"
#include "ble.h"
#include "EEPROM.h"
#include "eeprom_util.h"
#include "feedback_util.h"
#include "web_socket_client_util.h"
 
//#include "cpu0_task.h"

#define SERVOMIN 75
#define SERVOMAX 550

/************Instance definition*************/

void lqr_balance_loop();
void robot_sitdown();
void leg_loop();
void jump_loop();
void yaw_loop();
void web_loop();
void yaw_angle_addup();
void basicWebCallback(void);
void webSocketEventCallback(uint8_t num, WStype_t type, uint8_t* payload, size_t length);
void adc_calibration_init();
void bat_check();
void bat_led_blink();
bool one_second_tick(void);
bool ten_msec_tick(void);
uint16_t angleToPulse(int ang);

//Electromotor instance
BLDCMotor motor1 = BLDCMotor(7);
BLDCMotor motor2 = BLDCMotor(7);
BLDCDriver3PWM driver1 = BLDCDriver3PWM(32, 33, 25, 22);
BLDCDriver3PWM driver2 = BLDCDriver3PWM(26, 27, 14, 12);

//Encoder instance
TwoWire I2Cone = TwoWire(0);
TwoWire I2Ctwo = TwoWire(1);
MagneticSensorI2C sensor1 = MagneticSensorI2C(AS5600_I2C);
MagneticSensorI2C sensor2 = MagneticSensorI2C(AS5600_I2C);

//PID instance
/*PIDController pid_angle{ .P = 1, .I = 0, .D = 0, .ramp = 100000, .limit = 8 };
PIDController pid_gyro{ .P = 0.06, .I = 0, .D = 0, .ramp = 100000, .limit = 8 };
PIDController pid_distance{ .P = 0.5, .I = 0, .D = 0, .ramp = 100000, .limit = 8 };
PIDController pid_speed{ .P = 0.7, .I = 0, .D = 0, .ramp = 100000, .limit = 8 };
PIDController pid_yaw_angle{ .P = 1.0, .I = 0, .D = 0, .ramp = 100000, .limit = 8 };
PIDController pid_yaw_gyro{ .P = 0.04, .I = 0, .D = 0, .ramp = 100000, .limit = 8 };
PIDController pid_lqr_u{ .P = 1, .I = 15, .D = 0, .ramp = 100000, .limit = 8 };
PIDController pid_zeropoint{ .P = 0.002, .I = 0, .D = 0, .ramp = 100000, .limit = 4 };
PIDController pid_roll_angle{ .P = 8, .I = 0, .D = 0, .ramp = 100000, .limit = 450 };*/

PIDController pid_angle{ .P = 50.0, .I = 0, .D = 0, .ramp = 100000, .limit = 8 };
PIDController pid_gyro{ .P = 4.0, .I = 0, .D = 0, .ramp = 100000, .limit = 8 };
PIDController pid_distance{ .P = 0.3, .I = 0, .D = 0, .ramp = 100000, .limit = 4 };
PIDController pid_speed{ .P = 0.51, .I = 0, .D = 0, .ramp = 100000, .limit = 8 };
PIDController pid_yaw_angle{ .P = 1.0, .I = 0, .D = 0, .ramp = 100000, .limit = 8 };
PIDController pid_yaw_gyro{ .P = 0.7, .I = 0, .D = 0, .ramp = 100000, .limit = 8 };
PIDController pid_lqr_u{ .P = 1, .I = 30, .D = 0, .ramp = 100000, .limit = 8 };
PIDController pid_zeropoint{ .P = 0.00003508771f, .I = 0, .D = 0, .ramp = 100000, .limit = 4 }; // 
PIDController pid_roll_angle{ .P = 0, .I = 0, .D = 0, .ramp = 100000, .limit = 450 };

/*PIDController pid_angle{ .P = 30, .I = 0, .D = 0, .ramp = 100000, .limit = 8 };
PIDController pid_gyro{ .P = 2, .I = 0, .D = 0, .ramp = 100000, .limit = 8 };
PIDController pid_distance{ .P = 0, .I = 0, .D = 0, .ramp = 100000, .limit = 8 };
PIDController pid_speed{ .P = 0, .I = 0, .D = 0, .ramp = 100000, .limit = 8 };
PIDController pid_yaw_angle{ .P = 0, .I = 0, .D = 0, .ramp = 100000, .limit = 8 };
PIDController pid_yaw_gyro{ .P = 0, .I = 0, .D = 0, .ramp = 100000, .limit = 8 };
PIDController pid_lqr_u{ .P = 1, .I = 15, .D = 0, .ramp = 100000, .limit = 8 };
PIDController pid_zeropoint{ .P = 0.002, .I = 0, .D = 0, .ramp = 100000, .limit = 4 };
PIDController pid_roll_angle{ .P = 0, .I = 0, .D = 0, .ramp = 100000, .limit = 450 };*/

//Low pass filter instance
LowPassFilter lpf_joyy{ .Tf = 0.2 };
LowPassFilter lpf_zeropoint{ .Tf = 0.1 };
LowPassFilter lpf_roll{ .Tf = 0.3 };

// Commander instance
Commander command = Commander(Serial);

void StabAngle(char* cmd) {
  command.pid(&pid_angle, cmd);
}
void StabGyro(char* cmd) {
  command.pid(&pid_gyro, cmd);
}
void StabDistance(char* cmd) {
  command.pid(&pid_distance, cmd);
}
void StabSpeed(char* cmd) {
  command.pid(&pid_speed, cmd);
}
void StabYawAngle(char* cmd) {
  command.pid(&pid_yaw_angle, cmd);
}
void StabYawGyro(char* cmd) {
  command.pid(&pid_yaw_gyro, cmd);
}
void lpfJoyy(char* cmd) {
  command.lpf(&lpf_joyy, cmd);
}
void StabLqrU(char* cmd) {
  command.pid(&pid_lqr_u, cmd);
}
void StabZeropoint(char* cmd) {
  command.pid(&pid_zeropoint, cmd);
}
void lpfZeropoint(char* cmd) {
  command.lpf(&lpf_zeropoint, cmd);
}
void StabRollAngle(char* cmd) {
  command.pid(&pid_roll_angle, cmd);
}
void lpfRoll(char* cmd) {
  command.lpf(&lpf_roll, cmd);
}

bool sitdown_falg = false;

//void Stabtest_zeropoint(char* cmd) { command.pid(&test_zeropoint, cmd); }

//WebServer instance
WebServer webserver;                                // server
WebSocketsServer websocket = WebSocketsServer(81);  // Define a webSocket server to process messages sent by clients
int joystick_value[2];

// MPU6500 instance
IMU imu(&I2Ctwo);

// PCA9685 instance
Servos board;

/************parameter definition*************/
#define pi 3.1415927

//LQR Self-balancing controller parameters
float LQR_angle = 0;
float LQR_gyro = 0;
float LQR_speed = 0;
float LQR_distance = 0;
float angle_control = 0;
float gyro_control = 0;
float speed_control = 0;
float distance_control = 0;
float LQR_u = 0;
float angle_zeropoint = 0.9522 * DEG2RAD;// 0.9522 * DEG2RAD;//-1.48; 1.62
float distance_zeropoint = -256.0;  //Wheel position shift zero offset \
 (-256 is an impossible displacement value, use it as a sign that it is not refreshed)


//YAW axis control data
float YAW_gyro = 0;
float YAW_angle = 0;
float YAW_angle_last = 0;
float YAW_angle_total = 0;
float YAW_angle_zero_point = -10;
float YAW_output = 0;

//Leg steering gear control data
/*byte ID[2];
s16 Position[2];
u16 Speed[2];
byte ACC[2];*/

//Logical processing flag bit
float robot_speed = 0;          //Record the current wheel speed
float robot_speed_last = 0;     //Record the wheel speed at the previous time
int wrobot_move_stop_flag = 0;  //Record the sign that the rocker stops
int jump_flag = 0;              //Jump period identification
float leg_position_add = 0;     //roll axis balance control quantity

//Voltage detection

static const adc1_channel_t channel = ADC1_CHANNEL_7;
// static const adc_bits_width_t width = ADC_WIDTH_BIT_12;
static const adc_atten_t atten = ADC_ATTEN_DB_11;
static const adc_unit_t unit = ADC_UNIT_1;

//Power display LED Pin
#define LED_BAT 13

void user_function(char* cmd) {
  if (*cmd == '{') {
    rp.json_test(cmd);
  }
}

void setup() {
  Serial.begin(2000000);
  Serial2.begin(1000000);
  rp.get_pcb_version();
  rp.config_json_init();
  ble_init();
  wifi_init();
  if (get_wifi_state() != WIFI_STATE.CLOSE) {
    webserver.begin();
    webserver.on("/", HTTP_GET, basicWebCallback);
    websocket.begin();
    websocket.onEvent(webSocketEventCallback);
  }
  

  web_sockets_client_init();

  //xTaskCreatePinnedToCore(cpu0_task, "cpu0_task", 2048, NULL, 0, NULL, 0);

  //Steering gear initialization
  //Steering gear effective stroke 450
  //Left-hand steering gear[2048+12+50,2048+12+450]
  //Right-hand steering gear[2048-12-50,2048-12-450]
  /*sms_sts.pSerial = &Serial2;
  ID[0] = 1;
  ID[1] = 2;
  ACC[0] = 30;
  ACC[1] = 30;
  Speed[0] = 300;
  Speed[1] = 300;
  Position[0] = 2048;
  Position[1] = 2048;*/
  //The steering gear (ID1/ID2) runs to their respective positions at maximum speed V=2400 steps/SEC and \
  acceleration A=50(50*100 steps/SEC ^2)
  //sms_sts.SyncWritePosEx(ID, 2, Position, Speed, ACC);

  //Voltage detection
  adc_calibration_init();
  adc1_config_width(ADC_WIDTH_BIT_12);
  adc1_config_channel_atten(channel, atten);
  esp_adc_cal_characterize(unit, atten, ADC_WIDTH_BIT_12, 0, &adc_chars);

  //Voltage detection LED
  pinMode(LED_BAT, OUTPUT);

  // Encoder setup
  I2Cone.begin(19, 18, 400000UL);
  I2Ctwo.begin(23, 5, 400000UL);
  sensor1.init(&I2Cone);
  sensor2.init(&I2Ctwo);

  // ==========================================
  // MPU9250 setup & Calibração Manual
  // ==========================================
  //mpu9250.setWire(&I2Ctwo);
  //mpu9250.calibrate();
  imu.calibrate();
  // ==========================================

  //Connect the motor object to the encoder object
  motor1.linkSensor(&sensor1);
  motor2.linkSensor(&sensor2);

  //Speed loop PID parameter
  motor1.PID_velocity.P = 0.05;
  motor1.PID_velocity.I = 1;
  motor1.PID_velocity.D = 0;

  motor2.PID_velocity.P = 0.05;
  motor2.PID_velocity.I = 1;
  motor2.PID_velocity.D = 0;

  // Motor driver setup
  motor1.voltage_sensor_align = 6;
  motor2.voltage_sensor_align = 6;
  driver1.voltage_power_supply = 8;
  driver2.voltage_power_supply = 8;
  driver1.init();
  driver2.init();

  //Connect the motor object to the drive object
  motor1.linkDriver(&driver1);
  motor2.linkDriver(&driver2);

  motor1.torque_controller = TorqueControlType::voltage;
  motor2.torque_controller = TorqueControlType::voltage;
  motor1.controller = MotionControlType::torque;
  motor2.controller = MotionControlType::torque;

  // Motor-related Settings
  motor1.useMonitoring(Serial);
  motor2.useMonitoring(Serial);
  //init
  motor1.init();
  motor1.initFOC();
  motor2.init();
  motor2.initFOC();

  rp.m1_direction = motor1.sensor_direction == CW?  -0.5 : 0.5;
  rp.m2_direction = motor2.sensor_direction == CCW? -0.5 : 0.5;

  Serial.println("Motor1 direction:" + String(rp.m1_direction));
  Serial.println("Motor2 direction:" + String(rp.m2_direction));

  // Setup pca9685
  board.inicializarPCA9685();
  
  // Map motor to commander
  command.add('A', StabAngle, (char*) "pid angle");
  command.add('B', StabGyro, (char*) "pid gyro");
  command.add('C', StabDistance, (char*) "pid distance");
  command.add('D', StabSpeed, (char*) "pid speed");
  command.add('E', StabYawAngle, (char*) "pid yaw angle");
  command.add('F', StabYawGyro, (char*) "pid yaw gyro");
  command.add('G', lpfJoyy, (char*) "lpf joyy");
  command.add('H', StabLqrU, (char*) "pid lqr u");
  command.add('I', StabZeropoint, (char*) "pid zeropoint");
  command.add('J', lpfZeropoint, (char*) "lpf zeropoint");
  command.add('K', StabRollAngle, (char*) "pid roll angle");
  command.add('L', lpfRoll, (char*) "lpf roll");
  command.add('U', user_function, (char*) "user function");

  leg_loop(); 

  //command.add('M', Stabtest_zeropoint, "test_zeropoint");
  delay(500);
}

void loop() {

  if (one_second_tick()) {
    bat_check();  //Voltage detection
    wifi_loop();
    static int ttss;
    //Serial.println(ttss++);
  }
  if (ten_msec_tick()) {
    ble_loop();
    bat_led_blink();  //Voltage indication LED light
    rp.test_log_output();
    //Serial.print("Angle y: ");
    //Serial.println(imu.getAngleY() * RAD2DEG);

    static int leg_prescaler = 0;
    leg_prescaler++;
    if(leg_prescaler >= 4) {
      leg_loop(); 
      leg_prescaler = 0;
    }
  }

  web_loop();  //Web data update

  imu.updateMPU();    //IMU data update

  

  lqr_balance_loop();  //lqr self-balancing control
  yaw_loop();          //yaw axis steering control

  //The self-balancing calculated output torque is assigned to the motor
  motor1.target = -(LQR_u + YAW_output) * rp.m1_direction;
  motor2.target = -(LQR_u - YAW_output) * rp.m2_direction;
  //motor1.target = (LQR_u + YAW_output) * rp.m1_direction;
  //motor2.target = (LQR_u - YAW_output) * rp.m2_direction;
 
  

  //Shut down output after falling out of control
  
  if (abs(LQR_angle) > rp.uncontrollable_angle * DEG2RAD) {
    rp.uncontrollable = 1;
  }
  if (rp.uncontrollable != 0)  //Delay recovery after lifting
  {
    if (abs(LQR_angle) < rp.recovery_angle * DEG2RAD) {
      rp.uncontrollable++;
    }
    if (rp.uncontrollable > 200)  //The delay time of 200 program cycles
    {
     rp.uncontrollable = 0;
    }
  }

  
  if(wrobot.go == 0){
    //robot_sitdown();
  }else{
    sitdown_falg = false;
  }

  //Turn off output (remote control stop or Angle is too large out of control)
  if (rp.uncontrollable != 0) {
    sitdown_falg = true;
    motor1.target = 0;
    motor2.target = 0;
    leg_position_add = 0;
    wrobot.joyx = 0;
    wrobot.joyy = 0;
    wrobot.roll = 0;
    wrobot.height = 32;
  }

  //Record the last remote control data
  wrobot.dir_last = wrobot.dir;
  wrobot.joyx_last = wrobot.joyx;
  wrobot.joyy_last = wrobot.joyy;

  //The FOC phase voltage is computed iteratively
  motor1.loopFOC();
  motor2.loopFOC();

  //Set the wheel motor output
  motor1.move();
  motor2.move();

  command.run();
}

//lqr self-balancing control
void lqr_balance_loop() {
  /*
  * LQR balance formula, in order to facilitate the adjustment of parameters in actual use, 
  * the formula is decomposed into 4 P controls, 
  * using the PIDController method in commander real-time debugging
  */
  //QR_u = LQR_k1*(LQR_angle - angle_zeropoint) + LQR_k2*LQR_gyro + LQR_k3*(LQR_distance - distance_zeropoint) + LQR_k4*LQR_speed;

  //The negative value is given because, according to the current motor wiring, the positive torque will turn backwards
  LQR_distance = -(motor1.shaft_angle * rp.m1_direction + motor2.shaft_angle * rp.m2_direction);
  LQR_speed    = -(motor1.shaft_velocity * rp.m1_direction + motor2.shaft_velocity * rp.m2_direction);

  // PATCH A: inicializa distance_zeropoint no primeiro ciclo real
  /*static bool distance_initialized = false;
  if (!distance_initialized) {
      distance_zeropoint = LQR_distance;
      distance_initialized = true;
      return; // pula só o primeiríssimo ciclo da vida do robô
  }*/

  LQR_angle = imu.getAngleY();
  LQR_gyro = imu.getGyroY();
  angle_control = pid_angle(LQR_angle - angle_zeropoint);
  gyro_control = pid_gyro(LQR_gyro);

  //Motion detail optimization processing
  if (wrobot.joyy != 0)  //Handling when there are forward and backward direction motion instructions
  {
    distance_zeropoint = LQR_distance;  //Displacement zero reset
    pid_lqr_u.error_prev = 0;           //The output integral is cleared to zero
  }

  if ((wrobot.joyx_last != 0 && wrobot.joyx == 0) || (wrobot.joyy_last != 0 && wrobot.joyy == 0))  //Stop in place processing when motion instruction returns to zero
  {
    wrobot_move_stop_flag = 1;
  }
  if ((wrobot_move_stop_flag == 1) && (abs(LQR_speed) < 0.5)) {
    distance_zeropoint = LQR_distance;  //Displacement zero reset
    wrobot_move_stop_flag = 0;
  }

  if (abs(LQR_speed) > 15)  //Stop in place treatment when being pushed rapidly
  {
    distance_zeropoint = LQR_distance;  //Displacement zero reset
  }

  //Calculate displacement control output
  distance_control = pid_distance(LQR_distance - distance_zeropoint);
  speed_control = pid_speed(LQR_speed - 0.07 * lpf_joyy(wrobot.joyy));

  //Wheel lift detection
  robot_speed_last = robot_speed;  //Record two consecutive wheel speeds
  robot_speed = LQR_speed;
  if (abs(robot_speed - robot_speed_last) > 10 || abs(robot_speed) > 50 || (jump_flag != 0)) /*If the angular speed and angular acceleration of the 
                                                    wheel are too large or in the recovery period after jumping, 
                                                    it is considered that the wheel is off the 
                                                    ground and needs special treatment.
                                                  */
  {
    distance_zeropoint = LQR_distance;     //Displacement zero point reset
    LQR_u = angle_control + gyro_control;  //When the wheel part is off the ground, \
                                          the quantity of the opposite wheel part is not output.\
                                          Conversely, under normal conditions, the balanced torque is fully output
    pid_lqr_u.error_prev = 0;              //The output integral is reset to zero
  } else {
    LQR_u = angle_control + gyro_control + distance_control + speed_control;
  }

  //Trigger conditions: No signal input from the remote control, \
    normal intervention of the wheel position movement control, \
    and not in the recovery period after jumping
  if (abs(LQR_u) < 5 && wrobot.joyy == 0 && abs(distance_control) < 4 && (jump_flag == 0)) {

    LQR_u = pid_lqr_u(LQR_u);  //Compensate for the nonlinearity of small torque
    angle_zeropoint -= pid_zeropoint(lpf_zeropoint(distance_control));  //Center of gravity adaptive
  } else {
    pid_lqr_u.error_prev = 0;  //The output integral is reset to zero
  }

  //The balance control parameters are adaptive
  /*if(pid_speed.P > 0) {
    if (wrobot.height < 50) {
      pid_speed.P = 0.7;
    } else if (wrobot.height < 64) {
      pid_speed.P = 0.6;
    } else {
      pid_speed.P = 0.5;
    }
  }*/
}
void robot_sitdown()
{
  if(rp.uncontrollable != 0)
  { 
    return;
  }
  
  float _angle = LQR_angle - angle_zeropoint;
  //当前没有坐下，调整角度
  if(  _angle > (-1) && sitdown_falg == false )
  {
    wrobot.joyy = -100;
  }
  //此时身体已经为后仰，可以关闭动力，然后自然坐下
  else{
    sitdown_falg = true;
    motor1.target = 0;
    motor2.target = 0;
    leg_position_add = 0;
    wrobot.joyx = 0;
    wrobot.joyy = 0;
    wrobot.roll = 0;
    wrobot.height = 32;
  }
}
//Leg movement control
void leg_loop() {

  // 1. Roll em graus (mesma lógica)
  float roll_angle_deg = (imu.getAngleX() + rp.offset_roll) * RAD2DEG;
  leg_position_add = pid_roll_angle(lpf_roll(roll_angle_deg));

  // 2. Altura
  float max_height = 72.0f; 
  float flex_angle = (max_height - wrobot.height) * 1.2f; 
  if (flex_angle < 0) flex_angle = 0;

  // 3. Alvo final (Flexão + Equilíbrio Lateral)
  float left_leg_flex  = flex_angle - leg_position_add;
  float right_leg_flex = flex_angle + leg_position_add;

  // Limite de curso (evita partir a peça)
  left_leg_flex  = constrain(left_leg_flex, 0, 60);
  right_leg_flex = constrain(right_leg_flex, 0, 60);

  // 4. A LÓGICA ESPELHADA (Inspirada no en02)
  // Definimos a direção de cada servo baseada no seu (0, 180, 180, 0)
  // Se o servo 0 precisa de somar para dobrar, o servo 1 precisa de subtrair!
  int dir_s0 = 1;  // Para dobrar, vai em direção aos 90
  int dir_s1 = -1; // Para dobrar, desce do 180 em direção aos 90
  int dir_s2 = -1; // Espelho do S1
  int dir_s3 = 1;  // Espelho do S0

  board.setPWM_Software(0, angleToPulse(0   + (left_leg_flex  * dir_s0)));
  board.setPWM_Software(1, angleToPulse(180 + (left_leg_flex  * dir_s1)));
  
  board.setPWM_Software(2, angleToPulse(180 + (right_leg_flex * dir_s2)));
  board.setPWM_Software(3, angleToPulse(0   + (right_leg_flex * dir_s3)));

  /*// 1. O Pêndulo Lateral (Roll) - Evita que o robô caia de lado
  // Convertendo radianos para graus para o pid_roll_angle (P=8) ter força real
  float roll_angle_deg = (imu.getAngleX() + rp.offset_roll) * RAD2DEG;
  leg_position_add = pid_roll_angle(lpf_roll(roll_angle_deg));

  // 2. A Altura (Sit/Stand) baseado em pernas totalmente esticadas no topo
  // O wrobot.height padrão em pé é ~70, e sentado é 32.
  // Se a altura for máxima (ex: 72), a flexão é 0 (perna esticada).
  // Se a altura cair para 32, a flexão aumenta para dobrar a perna.
  float max_height = 72.0f; 
  float flex_angle = (max_height - wrobot.height) * 1.0f; // 1 grau por unidade de altura
  if (flex_angle < 0) flex_angle = 0; // Trava de segurança

  // 3. Combinando a flexão de altura com a compensação do Roll
  // Se o robô cair para a esquerda, leg_position_add fica positivo.
  // Queremos que a perna esquerda estique (flexione MENOS) -> subtrai leg_position_add
  // Queremos que a perna direita encolha (flexione MAIS) -> soma leg_position_add
  float left_leg_flex  = flex_angle - leg_position_add;
  float right_leg_flex = flex_angle + leg_position_add;

  // 4. Limites de segurança para não forçar a estrutura mecânica (ex: máx 70 graus de dobra)
  left_leg_flex  = constrain(left_leg_flex, 0, 70);
  right_leg_flex = constrain(right_leg_flex, 0, 70);

  // 5. Acionando os 4 Servos via PCA9685
  // Como (0, 180, 180, 0) é esticada, a flexão afasta o servo desse ponto:

  // PERNA ESQUERDA (Pinos 0 e 1)
  board.setPWM_Software(0, angleToPulse(0   + left_leg_flex));
  board.setPWM_Software(1, angleToPulse(180 - left_leg_flex));

  // PERNA DIREITA (Pinos 2 e 3)
  board.setPWM_Software(2, angleToPulse(180 - right_leg_flex));
  board.setPWM_Software(3, angleToPulse(0   + right_leg_flex));

  /*board.setPWM_Software(0, angleToPulse(0));
  board.setPWM_Software(1, angleToPulse(180));
  board.setPWM_Software(2, angleToPulse(180));
  board.setPWM_Software(3, angleToPulse(0));*/

  /*jump_loop();
  if (jump_flag == 0)  //Not in a jumping state
  {
    static s16 last_Position[2];
    //Adaptive control of the body height
    ACC[0] = 5;
    ACC[1] = 5;
    Speed[0] = 150;
    Speed[1] = 150;
    float roll_angle = (float)mpu6050.getAngleX() + rp.offset_roll;
    // leg_position_add += pid_roll_angle(roll_angle);
    leg_position_add = pid_roll_angle(lpf_roll(roll_angle));  //test
    Position[0] = 2048 + 8.4 * (wrobot.height - 32) - leg_position_add;
    Position[1] = 2048 - 8.4 * (wrobot.height - 32) - leg_position_add;
    if (Position[0] < 2110)
      Position[0] = 2110;
    else if (Position[0] > 2510)
      Position[0] = 2510;
    if (Position[1] < 1586)
      Position[1] = 1586;
    else if (Position[1] > 1986)
      Position[1] = 1986;

    if((last_Position[1] != Position[1])  || (last_Position[0] != Position[0]))
    {
      last_Position[0] = Position[0];
      last_Position[1] = Position[1];
      sms_sts.SyncWritePosEx(ID, 2, Position, Speed, ACC);
    }
    
  }*/
}
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

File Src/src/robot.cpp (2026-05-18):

#include "robot.h"
#include <ArduinoJson.h>
#include "wifi_robot.h"
#include "eeprom_util.h"
//#include "Servo_STS3032.h"
#include "SPIFFS.h"
#include <vector>
#include "cpu0_task.h"
#include "ble.h"
#include "web_socket_client_util.h"
#include <IMU.h>

int BAT_PIN = 35;
esp_adc_cal_characteristics_t adc_chars;
Wrobot wrobot;
RobotProtocol rp(20);

RobotProtocol::RobotProtocol(uint8_t len) {
  _len = len;
  _now_buf = new uint8_t[_len];
  _old_buf = new uint8_t[_len];

  for (int i = 0; i < _len; i++) {
    _now_buf[i] = 0;
  }

  _now_buf[0] = 0xAA;
  _now_buf[1] = 0x55;
}

RobotProtocol::~RobotProtocol() {
  delete[] _now_buf;
  delete[] _old_buf;
}

void RobotProtocol::spinOnce(void) {
  int flag = checkBufRefresh();
  if (flag) {
    //UART_WriteBuf(); //This will convert the control information on the web end into a serial port protocol for transmission

    //Serial.println(wrobot.dir);//Test data acquisition
    //Serial.println("date have send\n");
    //Serial.printf("height:%d\n", wrobot.height);
    //Serial.printf("roll:%d\n", wrobot.pitch);
    //Serial.printf("linear:%d\n", wrobot.linear);
    //        Serial.printf("\n");
    //        Serial.printf("joy_X:%d\n", wrobot.joyx);
    //        Serial.printf("joy_Y:%d\n", wrobot.joyy);
  }
}



/**************The following is simultaneously used for serial port output control protocols***************/

void RobotProtocol::UART_WriteBuf(void) {
  for (int i = 0; i < _len; i++) {
    Serial.write(_now_buf[i]);
  }
}

int RobotProtocol::checkBufRefresh(void) {
  int ret = 0;
  for (int i = 0; i < _len; i++) {
    if (_now_buf[i] != _old_buf[i]) {
      ret = 1;
      break;
    } else {
      ret = 0;
    }
  }

  for (int i = 0; i < _len; i++) {
    _old_buf[i] = _now_buf[i];
  }
  return ret;
}
// This undocumented internal function must be declared
extern "C" {
  uint8_t temprature_sens_read();
}

double RobotProtocol::get_pcb_version() {
  int sensorValue = analogRead(A0);
  pcb_version = sensorValue * (3.30 / 4096) + 1;
  Serial.print("pcb_version:");
  Serial.println(pcb_version);
  return pcb_version;
}

double RobotProtocol::get_fahrenheit() {
  return temprature_sens_read();
}

double RobotProtocol::get_degree_centigrade() {
  double fahrenheit = get_fahrenheit();
  // Convert to Celsius (unit: Fahrenheit)
  return (fahrenheit - 32) / 1.8;
}

double RobotProtocol::get_battery_voltage() {
  return battery_voltage;
}

double RobotProtocol::get_battery_level() {
  double currentVoltage = battery_voltage;
  double maxVoltage = 8.3;
  double minVoltage = 7.0;

  // Ensure the voltage is within a reasonable range

  if (currentVoltage >= maxVoltage) return 100.0;
  if (currentVoltage <= minVoltage) return 0.0;

  // Calculate the percentage
  double battery_percentage = (currentVoltage - minVoltage) / (maxVoltage - minVoltage) * 100.0;

  battery_percentage = round(battery_percentage) / 1;  // Format to retain two significant digits (rounded to 2 decimal places)

  // Battery logic correction (prevent out-of-bounds and display of 0 data)
  if (battery_percentage > 100) {
    battery_percentage = 100;
  } else if (battery_percentage < 1) {
    battery_percentage = 1;
  }
  battery_level = battery_percentage;
  return battery_percentage;
}

int RobotProtocol::get_robot_status() {
  // 0 - Normal state, 1 - Primary out-of-control state (tilting), 2 - Recovery waiting state
  int robot_status = -1;
  if (uncontrollable == 0) {
    robot_status = 0;
  } else if (uncontrollable == 1) {
    robot_status = 1;
  } else if (uncontrollable > 1) {
    robot_status = 2;
  }
  return robot_status;
}


void RobotProtocol::printDoc(StaticJsonDocument<300> &doc) {
  char receive_command[300];
  serializeJson(doc, receive_command);
  Serial.printf("receive_command:%s \r\n", receive_command);
}

bool create_and_write_file(const char *filePath, const char *content) {
  // Open the file in write mode (if the file does not exist, it will be created)
  File file = SPIFFS.open(filePath, FILE_WRITE);
  // Write the content to the file
  size_t bytesWritten = file.print(content);
  file.close();
  if (bytesWritten > 0) {
    Serial.printf("Successfully wrote %d bytes to the file\n", bytesWritten);
    return true;
  } else {
    Serial.println("An error occurred while writing to the file.");
    return false;
  }
}
void RobotProtocol::save_config_json(void) {

  char json_arr[CONFIG_JSON_SIZE + 1] = { 0 };
  serializeJson(rp.config_json, json_arr);

  //seve data
  eeprom_util.write(&EepromParam.ADDR_JSON, json_arr);

  //read data
  Serial.print("read config json :");Serial.println(eeprom_util.read(&EepromParam.ADDR_JSON));
}
void RobotProtocol::save_wifi_info_json(void) {
  
  char json_arr[WIFI_INFO_JSON_SIZE + 1] = { 0 };
  serializeJson(rp.wifi_info_json, json_arr);

  //seve data
  eeprom_util.write(&EepromParam.ADDR_WIFI_INFO_JSON, json_arr);

  //read data
  Serial.print("read wifi info json :");Serial.println(eeprom_util.read(&EepromParam.ADDR_WIFI_INFO_JSON));

}
void RobotProtocol::json_is_sys_wifi(StaticJsonDocument<300> &doc) {

  wifi_info_json[WIFI_INFO_KEY.STATE]     = doc[WIFI_INFO_KEY.STATE];
  if (doc[WIFI_INFO_KEY.STATE] == WIFI_STATE.CLIENT)
  {
    wifi_info_json[WIFI_INFO_KEY.SSID]      = doc[WIFI_INFO_KEY.SSID];
    wifi_info_json[WIFI_INFO_KEY.PASSWORD]  = doc[WIFI_INFO_KEY.PASSWORD];
  }

  // save data
  String jsonStr;
  serializeJson(wifi_info_json, jsonStr);
  eeprom_util.write(&EepromParam.ADDR_WIFI_INFO_JSON, jsonStr);

  // read data
  Serial.print("READ SAVE WEB SOCKET HOST:");
  Serial.println(eeprom_util.read(&EepromParam.ADDR_WIFI_INFO_JSON));
  wifi_restart();

}
void RobotProtocol::json_is_sys_web_socket_server(StaticJsonDocument<300> &doc) {
  String host = doc["host"];
  uint16_t port = doc["port"];
  String path = doc["path"];

  // save data
  eeprom_util.write(&EepromParam.ADDR_WEB_SOCKET_HOST, host);
  eeprom_util.writeUint16T(&EepromParam.ADDR_WEB_SOCKET_PORT, port);
  eeprom_util.write(&EepromParam.ADDR_WEB_SOCKET_PATH, path);

  // read data
  Serial.print("READ SAVE WEB SOCKET HOST:");
  Serial.println(eeprom_util.read(&EepromParam.ADDR_WEB_SOCKET_HOST));
  Serial.print("READ SAVE WEB SOCKET PORT:");
  Serial.println(eeprom_util.readToUint16T(&EepromParam.ADDR_WEB_SOCKET_PORT));
  Serial.print("READ SAVE WEB SOCKET PATH:");
  Serial.println(eeprom_util.read(&EepromParam.ADDR_WEB_SOCKET_PATH));
}
void RobotProtocol::json_is_sys_set_name(StaticJsonDocument<300> &doc) {
  if (doc["name"].isNull() == true) {
    Serial.println("Invalid json data.");
  } else {
    String name_str = doc["name"];
    if (name_str.length() > 20) {
      Serial.println("The name is too long. Please limit it to 20 characters or less.");
      return;
    }
    config_json[CONFIG_KEY.NAME] = doc["name"];
    save_config_json();
  }
}

// Interrupt function - This function will be called when the time is up.
void ARDUINO_ISR_ATTR show_expression_time_callback()
{
  rp.show_expression_time = -1;
}
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

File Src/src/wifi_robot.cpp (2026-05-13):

#include "wifi_robot.h"
#include "robot.h"
#include "eeprom_util.h"
#include "ble.h"

bool wifi_restart_flag = false;

WIFI_STATE_TypeDef WIFI_STATE;


// Configure the parameters related to the AP (hotspot) mode
// const char *ssid = "navbot-en01-xxxxxx";
const char *ap_password = "12345678";

IPAddress AP_IP(192, 168, 1, 11);
IPAddress AP_GATEWAY(192, 168, 1, 11);
IPAddress AP_SUBNET(255, 255, 255, 0);

char wifi_mode;


// ESP-01S access the WiFi network in AP mode
void wifi_set_sta() {
  //Read the wifi information
  String wifi_ssid = rp.wifi_info_json[WIFI_INFO_KEY.SSID];
  String wifi_password = rp.wifi_info_json[WIFI_INFO_KEY.PASSWORD];

  String dev_name = rp.config_json[CONFIG_KEY.NAME];
  const char* sta_name = dev_name.c_str();

  WiFi.setHostname(sta_name);
  wifi_mode = WIFI_STA;
  WiFi.mode(WIFI_STA);
  char* ssid_arr = (char*)wifi_ssid.c_str();
  char* password_arr = (char*)wifi_password.c_str();

  WiFi.begin(ssid_arr, password_arr);

  String wifi_info = String("ssid:") + wifi_ssid + ",password:" + wifi_password;
  Serial.println("Connecting to Wifi: " + wifi_info);
  Serial.printf("connect %s...\r\n", wifi_ssid);
}

void wifi_set_ap(void) {
  char ap_name[20] = { 0 };
  rp.build_dev_name(ap_name);
  wifi_mode = WIFI_AP;
  WiFi.mode(WIFI_AP);
  Serial.printf("Reset Reason: %d%%\n", ESP.getFreeHeap()*100 / ESP.getHeapSize());
  WiFi.softAPConfig(AP_IP, AP_GATEWAY, AP_SUBNET);
  Serial.printf("Reset Reason: %d%%\n", ESP.getFreeHeap()*100 / ESP.getHeapSize());
  WiFi.softAP(ap_name, ap_password);
  // Serial.println();
  // Serial.print("AP IP address = ");
  // Serial.println(WiFi.softAPIP());
}
bool is_wifi_state(String str)
{
  if(str == WIFI_STATE.CLIENT){
    return true;
  }else if(str == WIFI_STATE.SERVER){
    return true;
  }else if(str == WIFI_STATE.CLOSE){
    return true;
  }
  return false;
}
void get_wifi_info_json(void) {

  char state_arr[EepromParam.ADDR_WIFI_INFO_JSON.size];
  eeprom_util.read(&EepromParam.ADDR_WIFI_INFO_JSON, (char*)state_arr);
  String jsonStr = String(state_arr);
  deserializeJson(rp.wifi_info_json, jsonStr);

  if (is_wifi_state(rp.wifi_info_json[WIFI_INFO_KEY.STATE]) == false) {
    rp.wifi_info_json[WIFI_INFO_KEY.STATE] = WIFI_STATE.SERVER;
    rp.save_wifi_info_json();
  }
}
String get_wifi_state(void){
  String str = rp.wifi_info_json[WIFI_INFO_KEY.STATE];
  return str;
}

void wifi_init(void) {
  get_wifi_info_json();
  Serial.printf("wifi_state: %s\n", get_wifi_state());

  if (get_wifi_state() == WIFI_STATE.CLIENT) {
    Serial.println("start wifi client...");
    wifi_set_sta();  // wifi client
    rp.wifi_state = WIFI_CLIENT;
  } else if (get_wifi_state() == WIFI_STATE.SERVER) {
    Serial.println("start wifi server...");
    wifi_set_ap();  // wifi server
    rp.wifi_state = WIFI_SERVOR;
  } else {

  }
}
void wifi_restart(void)
{
  wifi_restart_flag = true;
}


bool wifi_status_now = false;
bool wifi_status_last = false;

bool wifi_connect_ok()
{
  return wifi_status_now;
}
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

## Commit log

2025-04-24 Modify SSID
    Modify the name of the hotspot，add sn code
2025-07-02 add screen
    [BodyBasc-Aluminum6061.stp, BodyBase-Steel.stp]
2025-07-17 JSON schema testing completed.
    to be completed ：
    get PCB version
2025-07-17 add pcb version info read
2025-07-17 update PCB image and add discord link
2025-07-18 Servo calibration waiting and JSON binding
    The operation has been verified through the serial port and is feasible. U1 stops the servo, U2 starts the servo, and U3 sets the current position to the midpoint.
2025-07-22 add calibrate servo JSON command
2025-07-24 Implementation of the “roll” Function in the Control Panel
2025-08-04 Add simulator files
    [base_visual.obj, leg_left_visual.obj, leg_right_visual.obj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]
2025-08-25 Bluetooth protocol corrects errors
    [ble.cpp, feedback_util.cpp, robot.cpp]
2025-09-03 expression set, cloud ctrl, servo set ID, servo calibrate
2025-09-04 Update Servo_STS3032.cpp
    Automatic standing code optimization
2025-09-06 Temporarily close the socket.The other logic has been completed and is awaiting retesting.
2025-09-09 Optimize the wheels and the lower legs
    Optimizing the wheels and lower legs of the robot can enable it to stand automatically.
    [crus1.stl, crus2.stl, wheel.stl]
2025-09-09 Revert "Features/20 auto standup"
    [new_crus1.stl, new_crus2.stl, new_wheel.stl]
2025-09-09 Leg model upload
    [new_curs1.stl, new_curs2.stl, new_wheel.stl]
2025-09-16 trim
    Complete the readme, Code optimization and function enhancement have been completed, but some data still need to be sorted out.
    [BOM_PCB_Controller.csv, BOM_PCB_Encoder.csv, BOM_PCB_IMU.csv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]
2025-09-22 Standardized process for calibrating the servo motor
2025-10-20 add magnet_frame.stl
    [magnet_frame.stl]
2025-10-27 The screen displays a low voltage warning. Add out-of-control angle adjustment
2025-11-07 Encoder interface adjustment, supporting automatic standing and sitting
    [Calf x1.stl, Calf_L x1.stl, Calf_MIR x1.stl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]
2025-12-09 Motor and LED optimization
    The motor does not require distinguishing the wire sequence. The flashing of the indicator light indicates the battery level.
2026-05-12 fix: replace broken/out-of-stock purchase links in BOM
    - Servo (B2): B0BP645PF9 (no offers available) -> B0GDTBX485 (S3032 in stock)
    - Screw M2.5x5 (B8): B0DDXRMGCW (temporarily out of stock) -> B01H2106US (in stock)
    [BOM.xlsx, BodyBasc-Aluminum6061.stp, Calf_L x1.stl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]
2026-05-13 Revert "fix: replace broken/out-of-stock purchase links in BOM"
    This reverts commit ca474354441eac0b973647561cb2cf2fc1119178.
    [BOM.xlsx, BodyBasc-Aluminum6061.stp, Calf_L x1.stl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]
2026-05-15 update IMU
2026-05-18 update pid
2026-05-20 update pid and angle zeropoint
2026-05-22 update leg loop
